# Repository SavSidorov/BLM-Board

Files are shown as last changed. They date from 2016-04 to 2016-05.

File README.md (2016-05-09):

*Copyright UBC Formula Electric 2016.* 

*This documentation describes Open Hardware and is licensed under the CERN OHL v1.2.*

*You may redistribute and modify this documentation under the terms of the [CERN OHL v1.2](http://ohwr.org/cernohl). This documentation is distributed WITHOUT ANY EXPRESS OR IMPLIED WARRANTY, INCLUDING OF MERCHANTABILITY, SATISFACTORY QUALITY, AND FITNESS FOR A PARTICULAR PURPOSE. Please see the CERN OHL v1.2 for applicable conditions.*

BLM_2017 - Rev. A 3D Render (Top)
*BLM_2017 - Rev. A 3D Render (Top)*

# Overview

The Brake Light Module (BLM_2017) is a brake light designed for our 2017 vehicle. It consists of a strip of 20 red chip LEDs and a Linear Technology LT3466 step-up LED driver.

The BLM is powered directly by the Drive Control Module (DCM_2017), which produces a +12V signal whenever either regenerative braking or the mechanical brakes are activated.

# Features & Specifications

- The LEDs are split into two series strings of 10, each powered by a separate channel on the LED driver. This allows the brake light to still be clearly seen even in the event of a failure of one of the strings.
- The LED driver switching frequency can be adjusted by changing the value of resistor R1, and the current through each string can be set by modifying the feedback resistors R2 and R3.
- The BLM can be powered from any DC source between approximately +3V to +18V. By default the current flowing through each of the two LED channels is set to 60mA (R2 = R3 = 3.3Ω), which results in a total measured power consumption of ≈ 2.8W and an input current of ≈ 240mA at +12V.
- The board has four M3 mounting holes arranged along its lower edge.
- The two power wires are soldered directly to dedicated pads on the board. The intention is for the BLM to be housed in a 3D-printed waterproof enclosure, thereby eliminating the need for a bulky waterproof board-mount connector on the PCB itself.

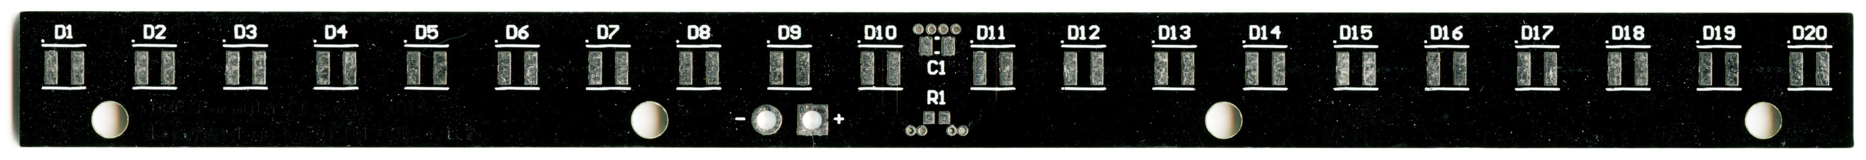
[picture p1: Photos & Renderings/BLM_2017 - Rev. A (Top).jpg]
BLM_2017 - Rev. A (Top)

*BLM_2017 - Rev. A (Top)*

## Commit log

2016-02-26 Add empty Altium Designer 14.3 project
    [BLM_2017.PcbDoc, BLM_2017.PcbLib, BLM_2017.PrjPcb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]
2016-02-27 [LIBRARIES] Add component to libraries
    - LED driver - Linear Technologies LT3466
    [BLM_2017.PcbLib, BLM_2017.SchLib]
2016-02-28 [Libraries] Add components to PCB library
    - Panasonic ERJ-Series
    - TDK C-Series (1608)
    - TDK C-Series (2012)
    [BLM_2017.PcbLib, BLM_2017.SchLib]
2016-03-09 Updated resistor and inductor values, changes the number of LEDs
    [BLM_2017.SchDoc]
2016-03-13 Updated resistors, inductor footprints, header, added LED footprints.
    [BLM_2017.PcbLib, BLM_2017.SchDoc]
2016-03-16 Fixed a few errors with the FB wires, Vin port, LED designations
    [BLM_2017.SchDoc, BLM_2017.SchLib]
2016-03-16 started PCB layout... need to make new board/size
    [BLM_2017.PcbDoc]
2016-03-16 [PCB] Modify board size
    [BLM_2017.PcbDoc]
2016-03-16 All PCB layout & routing done - EXCEPT C1B to left pad of LED10! (need to do this in layer 2)
    [BLM_2017.PcbDoc, BLM_2017.SchDoc]
2016-03-18 fixed the last few routes on the PCB file
    [BLM_2017.PcbDoc]
2016-03-19 Changed the board layout to make one long stip. still need to fix up a few last routes
    [BLM_2017.PcbDoc, BLM_2017.SchDoc]
2016-03-20 Rerouted some components, resized the board to save space
    [BLM_2017.PcbDoc]
2016-03-21 added drill holes
    [BLM_2017.PcbDoc, BLM_2017.SchDoc]
2016-03-25 Updated LED Footprint 3D body, fixed some text clearance errors
    [BLM_2017.PcbDoc, BLM_2017.PcbLib, BLM_2017.SchDoc]
2016-03-27 [Libraries] Modify component footprint in PCB library
    - OPTEK OVS5MxBCR4-Series
    [BLM_2017.PcbLib]
2016-03-27 [Libraries] Add component to PCB library
    - Bourns SRN4018-Series
    [BLM_2017.PcbLib]
2016-03-27 [Schematic] Check and reformat schematic
    [BLM_2017.SchDoc]
2016-03-27 [Schematic] Update feedback resistor values
    [BLM_2017.SchDoc]
2016-03-30 [PCB] Add design rules file
    [BLM_2017.PcbDoc]
2016-03-30 [Libraries] Modify components in PCB library
    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
    [BLM_2017.PcbLib, BLM_2017.SchLib]
2016-04-01 Added a grounding plane, still encountering a few bugs when running the DRC around the IC.
    [BLM_2017.PcbDoc, BLM_2017.PrjPcb]
2016-04-02 Changed pretty much everything. Still getting a lot of errors around the driver, due to the design rules. U1 designator needs to be moved, but for some reason I couldnt manage to move it.
    [BLM_2017.PcbDoc]
2016-04-11 [PCB] Replace LED footprint
    [BLM_2017.PcbDoc]
2016-04-11 [PCB] Modify component placement
    [BLM_2017.PcbDoc]
2016-04-13 [Libraries] Add component to schematic & PCB libraries
    - 2-Pin Bare Wire Pads
    [BLM_2017.PcbLib, BLM_2017.SchLib]
2016-04-15 [PCB] Update design rules file
2016-04-15 [PCB] Modify ground plane dimensions
    [BLM_2017.PcbDoc]
2016-04-17 [PCB] Export Rev. A bill of materials
    [BLM_2017 BOM - Rev. A.xlsx]
2016-04-18 [PCB] Add logos and board information to overlay
    [BLM_2017.PcbDoc]
2016-04-18 [PCB] Export 3D STEP model of PCB
    [BLM_2017 - Rev. A.step]
2016-04-18 [PCB] Export Rev. A Gerber files
    [BLM_2017.GBL, BLM_2017.GBO, BLM_2017.GBP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]
2016-04-19 Add schematic and board layout in PDF format
2016-04-19 [PCB] Add Rev. A 3D board renderings
2016-04-21 Add rules compliance spreadsheet
    [BLM_2017 Rules Compliance.xlsx]
2016-04-26 [PCB] Add Rev. A board scans
2016-04-27 Modify LED part number in BOM
    [BLM_2017 BOM - Rev. A.xlsx, BLM_2017.SchDoc]
2016-04-29 Update PDF schematic and board layout
2016-05-02 [README] Add Rev. A board scan
2016-05-04 [Schematic] Modify feedback resistor value
    [BLM_2017.SchDoc]
2016-05-04 [BOM] Update bill of materials
    - Replace feedback resistors
    [BLM_2017 BOM - Rev. A.xlsx]
2016-05-04 [README] Add power consumption data
2016-05-26 Update PDF of schematic and PCB layout
2018-10-06 Wiped repo, added gitignore file
    [BLM_2017 - Rev. A.step, BLM_2017 BOM - Rev. A.xlsx, BLM_2017 Rules Compliance.xlsx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]
